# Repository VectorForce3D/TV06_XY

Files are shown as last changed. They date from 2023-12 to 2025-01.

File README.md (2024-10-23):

# TV06
## A CoreXY conversion for the Sovol SV06 designed by Terminal Velocity

The TV06 is a conversion project aimed at bringing high speeds to SV06 3D printer owners. Originally developed as a branch of the ProosaXY, the TV06 has taken on a fully unique form now as it moves into full release. The goal of the machine is simple; 10k acceleration and 250mm/s print speeds at quality. While we have blown past these speeds now, we are working to improve kinematics to achieve even higher goals.

TV06r2_Front

## Discord
Please feel free to join our ever growing community. There are lots of help resources as well as experienced members ready to assist you with your build.
https://discord.gg/thxyRm7x9U

## Documentation
[WIP](https://terminal-velocity-knowledge-base.gitbook.io/tv06)

## File Nomenclature: A warning!
All of the files enclosed in the repo are titled very specifically! You MUST follow the instructions in each items title to achieve proper results. Failing to do so is likely to result in lots of failed prints and broken parts. 

### Key:
- STR = High strength profile; 3 walls @ 150% line width, 25% gyroid infill, 3 tops and bottoms, 0.4 nozzle is reccommended for proper fitment
- STD = Standard profile; print at your standard settings
- SUP = Enable Supports; we are doing our best to eliminate supports but are not quite there yet 
- NOSUP = Turn supports off
- AC/MAIN = Denotes accent color or main color
- 0X = Quantity of that model

### Example: Beam_R_STR_NOSUP_MAIN_4X.stl
This would denote a part that requires the high stength print profile and doesn't require support. Additionally, it is the main filament color of your choosing and you need to print four of them to satisfy this items requirement.

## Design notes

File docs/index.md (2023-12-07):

# TV06 CoreXY Conversion

The Terminal Velocity 06 project is a conversion project aimed at bringing high speeds to SV06 3D printer owners. Originally developed as a branch of the ProosaXY, the TV06 has taken on a fully unique form now as it moves into the Beta testing stage. The goal of the machine is simple; 10k acceleration and 250mm/s print speeds at quality.

TV06Transparent

The TV06 was designed by Dustmuffins and Ghoste of the TV06 Discord Server. We welcome all to our community and invite you to join our wonderful [community!](https://discord.gg/xVtU45zTrk).

???+ warning "Irreversible Alterations"

     The TV06 Project seeks to integrate numerous components from the original SV06 machine line, but certain compromises are unavoidable. Specifically, some elements, such as rods and leadscrews, will be cut during the modification process. The frame predominantly consists of new metal, and proficiency in using a metal saw is essential. If you lack experience in operating a metal saw, please reach out to our help-desk channel on [Discord](https://discord.gg/xVtU45zTrk), and someone will help you out.

## A thank you to our predecessor 

The TV06 project would not be where it is today without the initial time investments of the [ProosaXY](https://www.printables.com/model/518614-proosaxy-mk3s-to-corexy-conversion). We would like to thank Chip for their incredible work and inspiring us to make this project. 

Thank You

- TV06 Team

## Support Us

We couldn't do this without the love and support of our dedicated community! While we will never ask, donations are greatly accepeted and go directly to the TV06 project and furthering its development.

[Buy us a KoFi!](https://ko-fi.com/dustmuffins){ .md-button }

## Let's get started!

We're just as excited as you to get this build underway. We thank you for showing interest in our hardwork and without further ado, Let's Go!

[I'm Ready!](about.md){ .md-button .md-button--primary }

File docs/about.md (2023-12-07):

# First Steps

The first step to getting started with this build is understanding the filename nomenclature. We have specifically encoded every filename with a set of identifiers to ensure you print everything properly and in the correct color. 
We all know aesthetics are more important than function! Right?

## Nomenclature Key

| Key | Outcome |
| :---: | :---: |
| `STR` | High strength profile  |
| `STD` |  Standard profile |
| `SUP` | Enable Supports |
| `NOSUP` | Turn supports off |
| `AC/MAIN` | Denotes accent color or main color |
| `#X` | Quantity |

???+ info "High Strength vs Standard Strength"

    We recommend 2 Walls with 150% line width, 3 tops and bottoms with 0.20mm layer height, and 25% gyroid infill for our high strength parts. We are aware that old habits die hard and the Voron print specification is also acceptable, however we recommend trying ours as all parts were tested with these settings and not Voron specifications. Standard strength denotes 2-3 walls at standard line widths and enough tops, bottoms, and infill to not have any holes or pillowing. 

## Material Choice

We can not stress this enough; ASA is the material of choice for this machine. ABS is also just as acceptable however we have found ASA to be easier to print than ABS. Polymaker makes incredible ASA that has served us well across the duration of this project. Slightly pricier than others, it is absolutely worth the quality. If you are looking for a sightly more budget oriented option, flashforge makes decent ASA as well.

???+ danger "Do NOT Cut Corners"

    The above information is all to be followed to the letter. Do not risk damage to machine, property, or personal injury because you wanted to save a relatively insignificant amount of money by purchasing PLA, PETG, or not printing the parts at proper strength settings. Additionally, do not purchase white ASA or ABS from any brand. The pigment contains titanium dioxide which is known to weaken plastics noticeably. In conjunction with this, avoid eSun ABS+ for similar reasons. These will all come back to haunt you down the road and will significantly impact the longevity and performance of your machine.

    It is not worth the risk.

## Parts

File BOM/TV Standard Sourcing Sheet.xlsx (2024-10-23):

Category | Part | Qty | Specification | Link #1 | Link #2 | Link #3 | Description
Frame | 400mm 2020 Extrusion | 9 | Any Profile | https://us.misumi-ec.com/vona2/detail/110302683830/ | https://www.amazon.com/dp/B09SGNG9C6?ref=ppx_yo2ov_dt_b_product_details&th=1 |  | Main frame components
Frame | 330mm 2020 Extrusion | 4 | Any Profile | https://us.misumi-ec.com/vona2/detail/110302683830/ | https://www.amazon.com/dp/B09SGNG9C6?ref=ppx_yo2ov_dt_b_product_details&th=1 |  | Main frame components
Frame | 310mm 2020 Extrusion | 2 | Any Profile | https://us.misumi-ec.com/vona2/detail/110302683830/ | https://www.amazon.com/dp/B09SGNG9C6?ref=ppx_yo2ov_dt_b_product_details&th=1 |  | Main frame components
Frame | 500mm 2020 Extrusion | 2 | Any Profile | https://us.misumi-ec.com/vona2/detail/110302683830/ | https://www.amazon.com/dp/B09SGNG9C6?ref=ppx_yo2ov_dt_b_product_details&th=1
Frame | 370mm 2020 Extrusion | 2 | Any Profile | https://us.misumi-ec.com/vona2/detail/110302683830/ | https://www.amazon.com/dp/B09SGNG9C6?ref=ppx_yo2ov_dt_b_product_details&th=1 |  | Main frame components
Frame | 200mm 2020 Extrusion | 2 | Any Profile | https://us.misumi-ec.com/vona2/detail/110302683830/ | https://www.amazon.com/dp/B09SGNG9C6?ref=ppx_yo2ov_dt_b_product_details&th=1 |  | Main frame components
Frame | 338mm Mellow Carbon Tube | 1 | Mellow Vz 235 | [Link too long, click me] (https://www.aliexpress.us/item/3256804164357594.html) |  |  | X Gantry
Frame | Or
Frame | 338mm 2020 Misumi Profile | 1 | Misumi | https://us.misumi-ec.com/vona2/detail/110302683830/ |  |  | X Gantry Alternative
Hardware | M5x8 Button Head | 24 | Button Head | [Link too long, click me] (https://www.aliexpress.us/item/2251832624537980.html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) | Screws On Ali (https://www.aliexpress.us/item/2251832624537980.html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) |  | Frame Hardware
Hardware | M5x20 Button Head | 4 | Button Head | [Link too long, click me] (https://www.aliexpress.us/item/2251832624537980.html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) | Screws On Ali (https://www.aliexpress.us/item/2251832624537980.html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) |  | Frame Hardware
Hardware | M5x12 Socket Head Cap | 8 | Socket Cap | [Link too long, click me] (https://www.aliexpress.us/item/3256803421528528.html) | Screws On Ali (https://www.aliexpress.us/item/2251832624557792.html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)
Hardware | M5x35 Socket Head Cap | 8 | Socket Cap | [Link too long, click me] (https://www.aliexpress.us/item/3256803421528528.html) | Screws On Ali (https://www.aliexpress.us/item/2251832624557792.html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)
Hardware | M5x16 Socket Head Cap | 4 | Socket Cap | [Link too long, click me] (https://www.aliexpress.us/item/3256803421528528.html) | Screws On Ali (https://www.aliexpress.us/item/2251832624557792.html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)
Hardware | M4x12 Socket Head Cap | 12 | Socket Cap | [Link too long, click me] (https://www.aliexpress.us/item/3256803421528528.html) | Screws On Ali (https://www.aliexpress.us/item/2251832624557792.html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)
Hardware | M4x8 Socket Head Cap | 76 | Socket Cap | [Link too long, click me] (https://www.aliexpress.us/item/3256803421528528.html) | Screws On Ali (https://www.aliexpress.us/item/2251832624557792.html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)
Hardware | M3x8 Socket Head Cap | 150 | Socket Cap | [Link too long, click me] (https://www.aliexpress.us/item/3256803421528528.html) | Screws On Ali (https://www.aliexpress.us/item/2251832624557792.html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)
Hardware | M3x10 Socket Head Cap | 45 | Socket Cap | [Link too long, click me] (https://www.aliexpress.us/item/3256803421528528.html) | Screws On Ali (https://www.aliexpress.us/item/2251832624557792.html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)
Hardware | M3x12 Socket Head Cap | 26 | Socket Cap | [Link too long, click me] (https://www.aliexpress.us/item/3256803421528528.html) | Screws On Ali (https://www.aliexpress.us/item/2251832624557792.html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)
Hardware | M3 Assortment | 1 | Socket Cap | https://a.co/d/0elFNilK
Hardware | M4 Assortment | 1 | Socket Cap | https://a.co/d/04KYN5Kn
Hardware | M3x12 Flat Head | 4 |  | Provided
Hardware | M3x8 Flat Head | 2 |  | Provided
Hardware | M3 HeatSet | 100 | OD 4.5 / L 4 | [Link too long, click me] (https://www.aliexpress.us/item/3256804349544912.html)
Hardware | M4 HeatSet | 50 | OD 5.5 / L 4 | [Link too long, click me] (https://www.aliexpress.us/item/3256804349544912.html)
Hardware | M5 HeatSet | 20 | OD 7 / L 5 | [Link too long, click me] (https://www.aliexpress.us/item/3256804349544912.html)
Hardware | M3 T Nut Hammerhead | 150 | ISO 20 | [Link too long, click me] (https://www.aliexpress.us/item/3256803706450684.html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)
Hardware | M4 T Nut Hammerhead | 100 | ISO 20 | [Link too long, click me] (https://www.aliexpress.us/item/3256803706450684.html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)
Electronics | Mainboard | 1 | Sovol | Provided
Electronics | 4010 Radial Fan | 1 | Sovol | Provided |  |  | Hotend Fan
Electronics | 350w PSU | 1 | Sovol | Provided
Electronics | Nema 17 Drive Motors | 4 | Sovol | Provided
Electronics | SV06 Toolhead | 1 | Sovol | Provided
Electronics | Extended Z Stepper Y Cable | 1 | JST-XH | [Link too long, click me] (https://www.aliexpress.us/item/3256805055141467.html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)
Electronics | GDSTime 5015 Blower | 2 | 12v/24v | [Link too long, click me] (https://www.aliexpress.us/item/2251832587030279.html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) | [Link too long, click me] (https://www.amazon.com/GDSTIME-Brushless-Bearing-Cooling-Extruder/dp/B0B1V6JTB8) |  | Cooling Fan
Motion | 400mm 8mm linear rod | 2 | Sovol | Provided
Motion | SV06 X Linear Rods | 2 | Sovol | Provided
Motion | SV06 Y Linear Rod | 2 | Sovol | provided
Motion | Fushi F695 Bearing | 2 | 10 Pack | [Link too long, click me] (https://www.aliexpress.us/item/2251832664674464.html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) | [Link too long, click me] (https://www.amazon.com/F695-2RS-Bearing-5x13x4mm-Miniature-Bearings/dp/B07VMJLXLH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) |  | Idlers
Motion | GT2 Idler Toothed | 2 | W 7mm with t | [Link too long, click me] (https://www.aliexpress.us/item/2251832836818881.html) |  |  | Idlers
Motion | 5M GT2 6mm Belt | 1 | L5M W6mm | [Link too long, click me] (https://www.aliexpress.us/item/3256806321466333.html?gatewayAdapt=glo2usa4itemAdapt) | https://www.amazon.com/Upgrade-Non-Slip-Version-Printer-Printers/dp/B08R93QQ8Z |  | Drive Belt
Motion | LM8UU Linear Bearing | 4 | Sovol | Provided | Fushi Bearings [OUR CHOICE] (https://www.aliexpress.us/item/2251832657203612.html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) |  | Z Bearings
Motion | LM8LUU Linear Bearing | 2 | Fushi | Fushi Bearings [OUR CHOICE] (https://www.aliexpress.us/item/2251832692290166.html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) | https://www.amazon.com/Printer-Bearings-JGAurora-LM08LUU-LM8LUU/dp/B083XQTH41 |  | Y Bearings
Motion | 235mm Heated Bed Assembly | 1 | Sovol | Provided | New Bed if needed (https://www.aliexpress.us/item/3256805691880025.html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)
Motion | MGN9H 300mm Linear Rail | 1 | Z1 or Z2 Preload | CNA Rails (https://www.aliexpress.us/item/2251832586981749.html) | West3D Berserker [OUR CHOICE] (https://west3d.com/products/west3d-printing-mgn9h-1r-300-350-400-linear-rails-with-carriages-cna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) | Youmetong Rails (https://www.aliexpress.us/item/3256801245010834.html?scm_id=1007.24625.271276.0&scm-url=1007.24625.271276.0) | X Axis
Filament | 2kg ASA | 1 | Main Color | https://us.polymaker.com/products/polylite-asa | https://www.amazon.com/FLASHFORGE-Filament-Dimensional-Accuracy-Printing/dp/B09V7HG9DR |  | Printed Parts
Filament | 1kg ASA | 1 | Accent Color | https://us.polymaker.com/products/polylite-asa | https://www.amazon.com/FLASHFORGE-Filament-Dimensional-Accuracy-Printing/dp/B09V7HG9DR |  | Printed Parts

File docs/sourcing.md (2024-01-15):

## It's Alive!
This sourcing guide is a living, breathing document and should be viewed as such. The purpose of the sourcing guide is to help builders to locate parts as quickly and easily as possible. We understand that links go dead quite often as sellers pull and relist listings all the time. Please report any issues with seller links you find directly to us under the dead-links channel in our discord.

???+ warning "We're not finished!"

    This is NOT currently an exhaustive list of components. We are working towards this, but this takes time. We have limited resources and this is certainly a WIP. 

<div style="text-align: center"><iframe src="https://docs.google.com/spreadsheets/d/e/2PACX-1vRDuzh9zTTb0Dr3VAwCe3eVq7Pyc6kqRn8ZqNsRaBrNnAQ9p_Byug8odcZ4Mtml6v6jA4KULE2Pz__y/pubhtml;headers=false" frameborder="0" width="100%" height="1000" scrolling="no"></iframe></div>

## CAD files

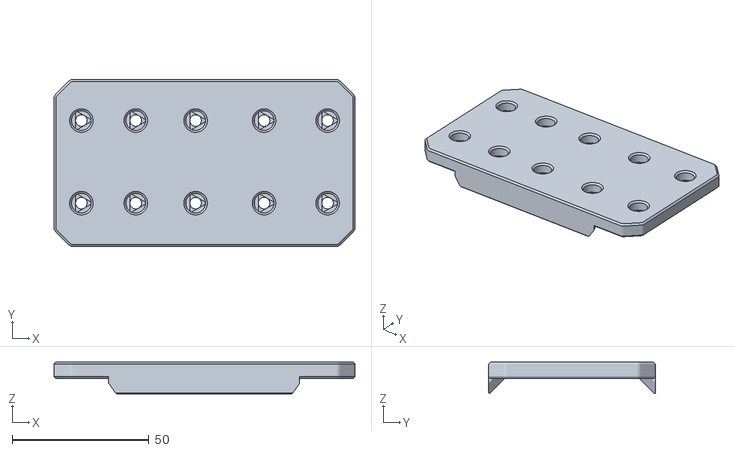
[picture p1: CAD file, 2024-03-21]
STL/Gantry/B_Drive/MotorMountRetensionPlate[B]_STR_NOSUP_MAIN_1X.STL
110.0 x 61.0 x 11.6

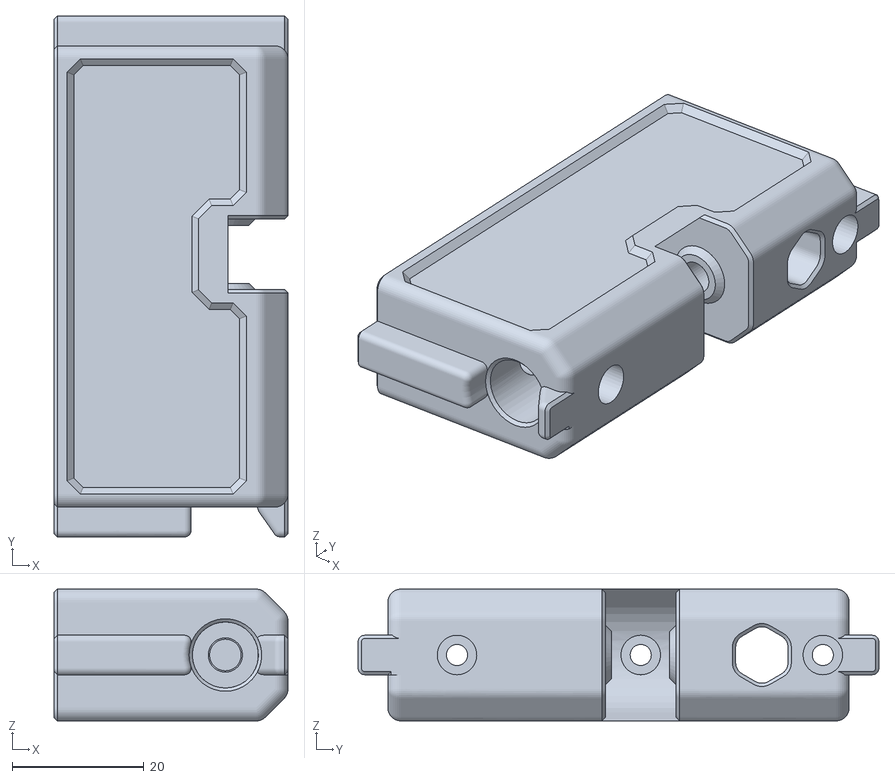
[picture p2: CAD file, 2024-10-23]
STL/Gantry/frontidlertower_r_str_nosup_main_1x.stl
35.5 x 79.0 x 20.0

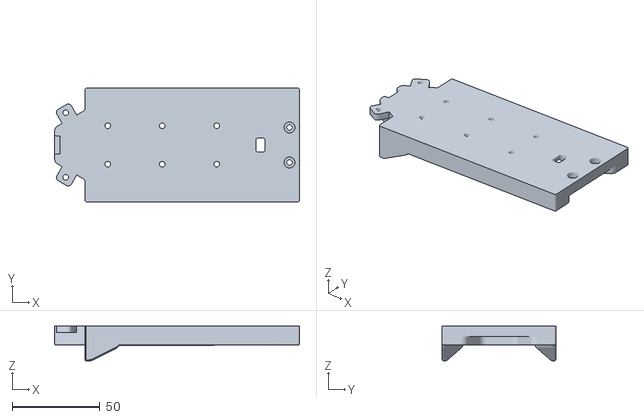
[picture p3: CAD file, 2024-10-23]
STL/Skirts/sideskirt_std_nosup_main_2x.stl
140.0 x 65.0 x 20.0

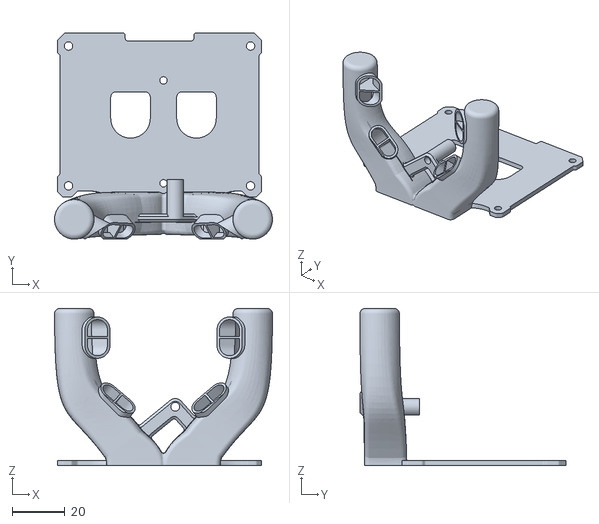
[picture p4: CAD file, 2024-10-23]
STL/Toolhead/QuadroDuct_Short_STR_SUP_MAIN_1X.stl
82.6 x 78.1 x 59.6

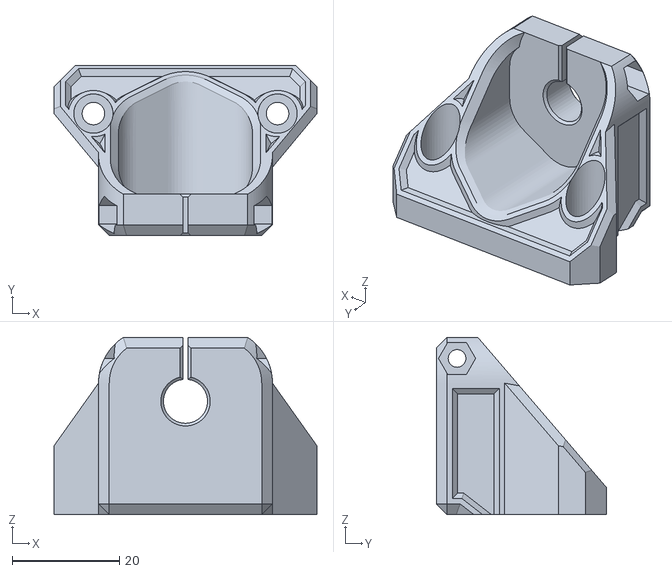
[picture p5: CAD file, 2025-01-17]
STL/Z_Assembly/lowerrodmount_str_nosup_main_4x.stl
49.0 x 31.8 x 33.0

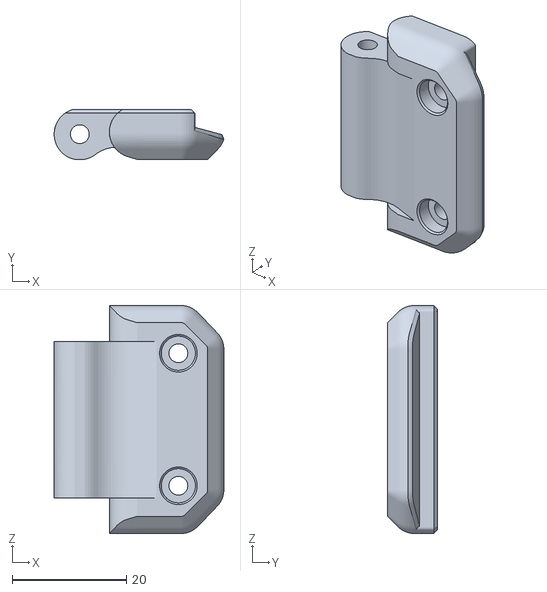
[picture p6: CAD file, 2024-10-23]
STL/Enclosure/hingebody_str_nosup_main_4x.stl
29.8 x 8.71 x 40.0

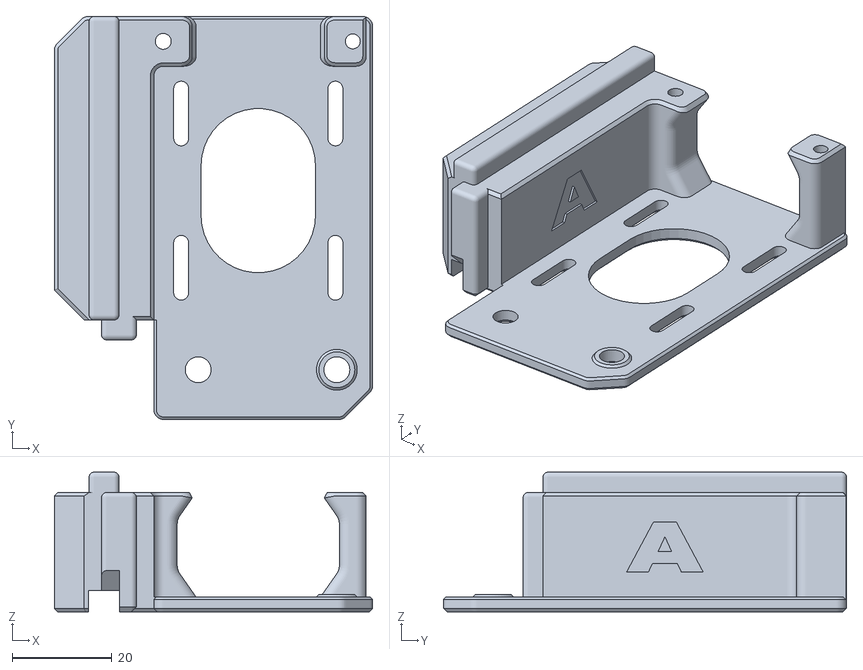
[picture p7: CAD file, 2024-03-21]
STL/Gantry/A_Drive/MotorPlate_Mid_A_Drive_STR_NOSUP_MAIN_1X.STL
64.0 x 81.0 x 28.1

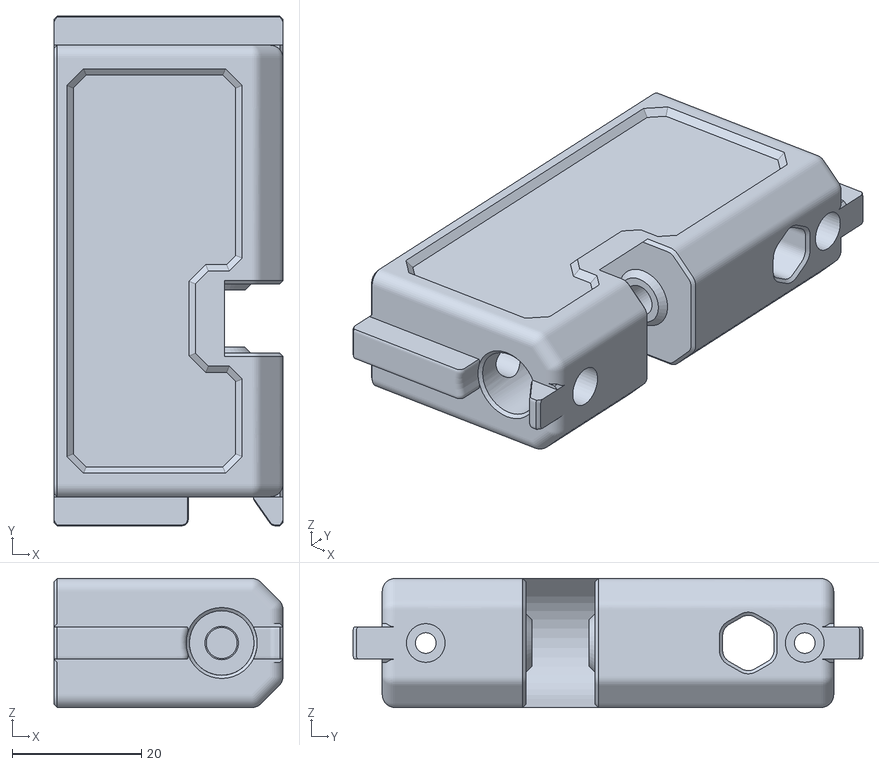
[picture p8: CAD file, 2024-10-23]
STL/Gantry/frontidlertower5mm_l_str_nosup_main_1x.stl
35.5 x 79.0 x 20.0

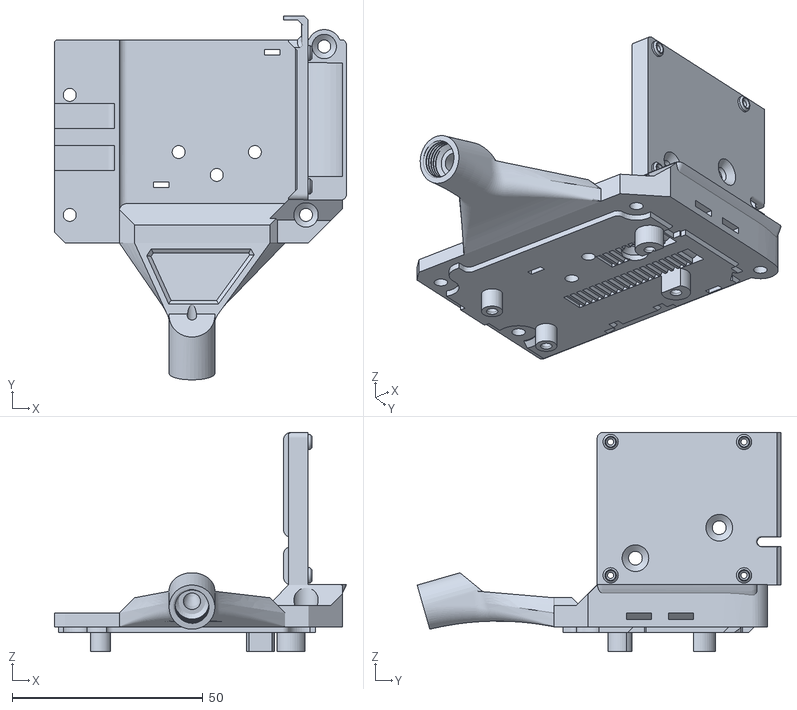
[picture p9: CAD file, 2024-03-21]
STL/Toolhead/BodyPlate_STR_SUP_MAIN_1X.STL
76.6 x 95.4 x 57.5

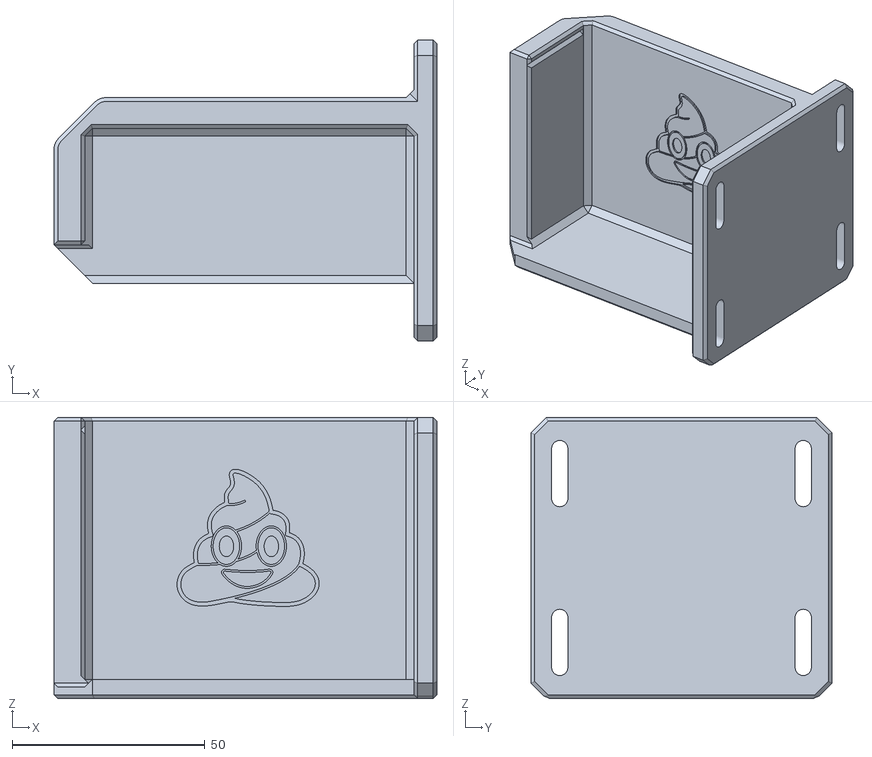
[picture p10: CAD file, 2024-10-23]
STL/Frame/purge_bucket_mount2_str_main_1x.stl
99.4 x 78.2 x 73.0

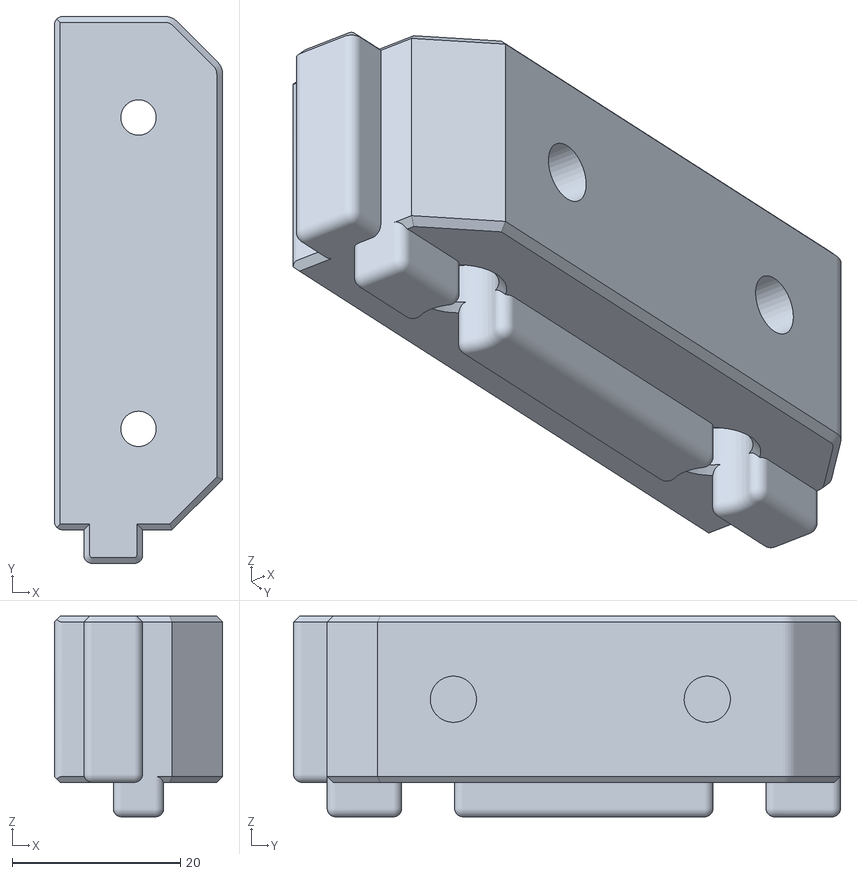
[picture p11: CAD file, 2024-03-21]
STL/Gantry/A_Drive/MotorPlate_Bottom_A_Drive_STR_NOSUP_MAIN_1X.STL
20.0 x 65.0 x 23.8

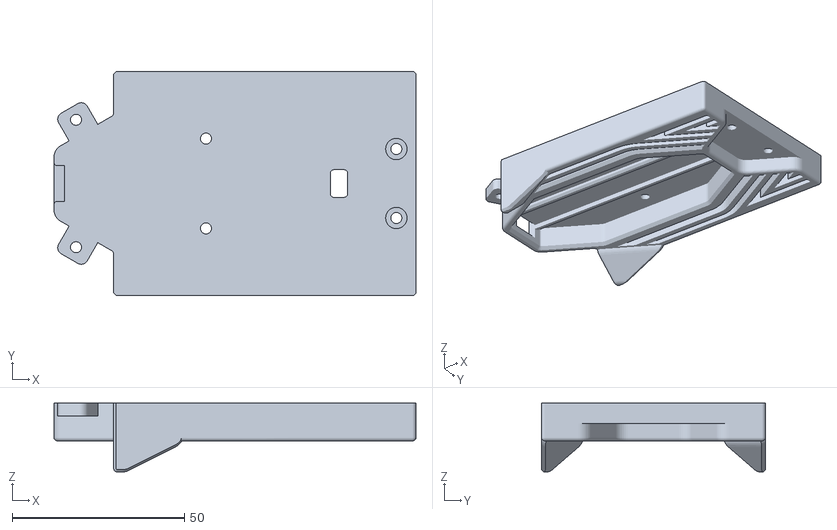
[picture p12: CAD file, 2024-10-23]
STL/Skirts/frontskirt_std_nosup_main_2x.stl
105.0 x 65.0 x 20.0

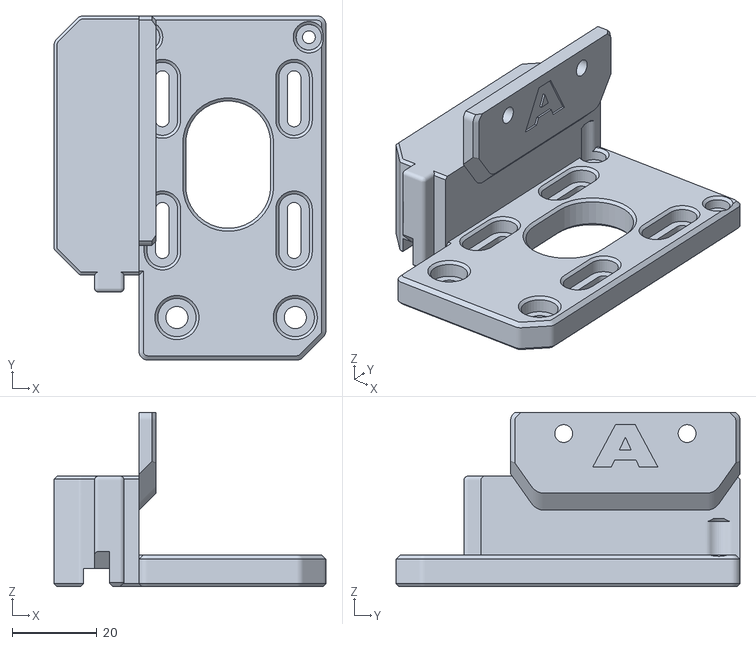
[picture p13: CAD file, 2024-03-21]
STL/Gantry/A_Drive/MotorPlate_Top_A_Drive_STR_NOSUP_MAIN_1X.STL
64.0 x 81.0 x 41.1

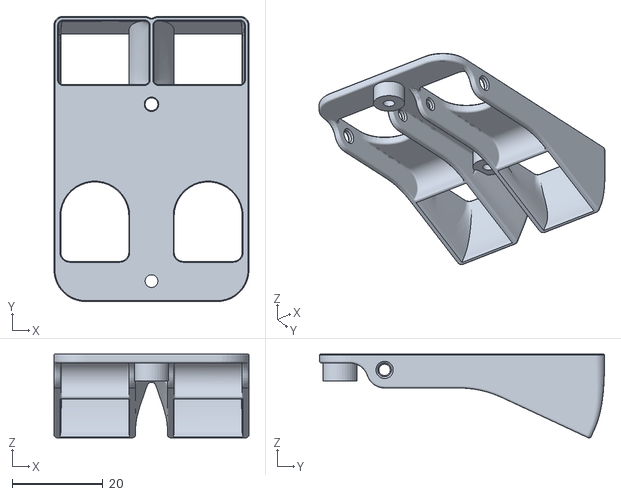
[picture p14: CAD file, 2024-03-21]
STL/Toolhead/Dual5015Mount_STR_NOSUP_MAIN_1X.STL
43.0 x 62.9 x 18.5

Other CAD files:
STL/Gantry/B_Drive/MotorPlate_Bottom_B_Drive_STR_NOSUP_MAIN_1X.STL
STL/Gantry/frontidlertower_l_str_nosup_main_1x.stl
STL/Gantry/B_Drive/MotorPlate_Top_B_Drive_STR_NOSUP_MAIN_1X.STL
STL/Gantry/frontidlertower5mm_r_str_nosup_main_1x.stl
DXF/TV06R2_Panels.step
DXF/[1x][ACM]Floor_Panel.dxf
DXF/[1x][ACM]Rear_Panel.dxf
DXF/[1x][PC_ACR]Top_Panel.dxf
DXF/[2x][PC_ACR]Door_Panel.dxf
DXF/[2x][PC_ACR]Side_Panel.dxf
STL/AWD/11mm_Spacer_2X.stl
STL/AWD/1mm_Spacer_10X.stl
STL/AWD/6mm AWD XY joint right a.stl
STL/AWD/6mm AWD XY joint right b.stl
STL/AWD/6mm AWD XY joint right c.stl
STL/AWD/FL_Bottom.stl
STL/AWD/FL_Top.stl
STL/AWD/FR_Bottom.stl
STL/AWD/FR_Top.stl
STL/AWD/Pin_Support_2X.stl
STL/AWD/RL_Bottom.stl
STL/AWD/RL_Top.stl
STL/AWD/RR_Bottom.stl
STL/AWD/RR_Top.stl
STL/AWD/Tensioner_2X.stl
STL/AWD/Y_Car_1_2X.stl
STL/AWD/Y_Car_2_2X.stl
STL/AWD/Y_Car_3_2X.stl
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

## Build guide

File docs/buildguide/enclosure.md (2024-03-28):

## Enclosure Design

Enclosure

## Bill of Materials
   | Item | Name | Quantity |
   | :---: | :---: | :----: |
   | `1` | M3x8 SHCS | 27 |
   | `2` | M3x10 SHCS | 12 |
  | `3` | M3x12 SHCS | 8 |
  | `4` | PanelClamp.stl | 27 |
   | `5` | Enclosure Door | 2 |
   | `6` | Enclosure Side Panel | 2 |
  | `7` | Enclosure Top Panel | 1 |
  | `8` | Enclosure Rear Panel | 1 |

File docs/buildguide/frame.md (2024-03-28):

## Frame Design
We created our frame to be simple and straightforward, eliminating the need for brackets or obscure corner attachments. Instead, we opted for blind joints because of their exceptional strength and rigidity. What sets them apart is not just their performance but also their affordability—a high-strength option at a low cost.

Frame

???+ warning "Buy The Right Extrusion!"

    Not all aluminum extrusion is created equally. Check your suppliers profile dimensions for the inner circular whole diameter. This MUST be smaller than 5mm so that we are able to tap the whole for an M5 thread which is about 4.8mm wide. 4.2mm hole is the prefered outer diameter of the center hole.

## Bill of Materials
=== "Carbon X Gantry"

    | Item | Name | Quantity |
    | :---: | :---: | :----: |
    | `1` | 400mm 2020 Extrusion | 9 |
    | `2` | 330mm 2020 Extrusion | 4 |
    | `3` | 310mm 2020 Extrusion | 2 |
    | `4` | 500mm 2020 Extrusion | 2 |
    | `5` | 370mm 2020 Extrusion | 2 |
    | `6` | 200mm 2020 Extrusion | 2 |
    | `7` | 338mm Mellow Carbon Tube | 1 |
    | `8` | M5x8 Button Head | 30 |
    | `9` | M5x20 Button Head | 4 |
    | `10` | M4x8 Socket Head Cap | 4 |
    
=== "Alu Tube X Gantry"

    | Item | Name | Quantity |
    | :---: | :---: | :----: |
     | `1` | 400mm 2020 Extrusion | 9 |
    | `2` | 330mm 2020 Extrusion | 4 |
    | `3` | 310mm 2020 Extrusion | 2 |
    | `4` | 500mm 2020 Extrusion | 2 |
    | `5` | 370mm 2020 Extrusion | 2 |
    | `6` | 200mm 2020 Extrusion | 2 |
    | `7` | 300mm 20mm 2mm Wall Aluminum Square Tube | 1 |
    | `8` | M5x8 Button Head | 30 |
    | `9` | M5x20 Button Head | 4 |
    | `10` | M4x8 Socket Head Cap | 4 |

???+ info "Carbon or Alu X Gantry?"

    As of right now, we recommend everyone purchase the carbon gantry. While it does add costs, it will offer the best results. There are also seperate Y Blocks that must be used to run the Alu gantry.

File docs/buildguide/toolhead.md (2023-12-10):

## What's new?
The SV06 is known for it's superior extrusion quality and compact toolhead size. We reused the stock toolhead with some modified parts to ensure that we brought this pedigree of perfection over to our machine. Namely, a major cooling upgrade was due for these increased speeds.

Toolheadfixed
## Bill of Materials
=== "Dual 5015"

    | Item        | Name | Quantity | Printable |
    | :---------: | ---- | :--: | ---- |
    | `1` | SV06 Stock Extruder | 1 | No |
    | `2` | [BackBeltPlate_STR_NOSUP_ANY_1X.stl](https://github.com/VectorForce3D/TV06_XY/raw/main/STL/Toolhead/BackBeltPlate_STR_NOSUP_ANY_1X.stl) | 1 | Yes |
    | `3` | [Double5015Mount_STD_NOSUP_MAIN_1X.stl](https://github.com/VectorForce3D/TV06_XY/raw/main/STL/Toolhead/Double5015Mount_STD_NOSUP_MAIN_1X.stl) | 1 | Yes |
    | `4` | MGN9H 300mm | 1 | No |
    | `5` | [ExtruderMount_STR_SUP_MAIN_1X.stl](https://github.com/VectorForce3D/TV06_XY/raw/main/STL/Toolhead/ExtruderMount_STR_SUP_MAIN_1X.stl) | 1 | Yes |
    | `6` | [FrontBeltPlate_STR_NOSUP_AC_1X.stl](https://github.com/VectorForce3D/TV06_XY/raw/main/STL/Toolhead/FrontBeltPlate_STR_NOSUP_AC_1X.stl) | 1 | Yes |
    | `7` | [MonolithicRailMount_STR_NOSUP_AC_1X.stl](https://github.com/VectorForce3D/TV06_XY/raw/main/STL/Toolhead/MonolithicRailMount_STR_NOSUP_AC_1X.stl) | 1 | Yes |
    | `8` | [StockNozzleAirDuct_STD_NOSUP_MAIN_1X.stl](https://github.com/VectorForce3D/TV06_XY/raw/main/STL/Toolhead/StockNozzleAirDuct_STD_NOSUP_MAIN_1X.stl) | 1 | Yes |
    | `9` | M3x12 Flathead | 4 | No |
    | `10` | M3x8 | 5 | No |
    | `11` | M3x8 Flathead | 2 | No |
    | `12` | M3x12 Flathead | 4 | No |
    | `13` | GDSTime 5015 12v Blower | 2 | No |

=== "4028 Radial Fan"

    | Item        | Name | Quantity | Printable |
    | :---------: | ---- | :--: | ---- |
    | `1` | SV06 Stock Extruder | 1 | No |
    | `2` | [BackBeltPlate_STR_NOSUP_ANY_1X.stl](https://github.com/VectorForce3D/TV06_XY/raw/main/STL/Toolhead/BackBeltPlate_STR_NOSUP_ANY_1X.stl) | 1 | Yes |
    | `3` | 4028Mount.stl | 1 | Yes |
    | `4` | MGN9H 300mm | 1 | No |
    | `5` | [ExtruderMount_STR_SUP_MAIN_1X.stl](https://github.com/VectorForce3D/TV06_XY/raw/main/STL/Toolhead/ExtruderMount_STR_SUP_MAIN_1X.stl) | 1 | Yes |
    | `6` | [FrontBeltPlate_STR_NOSUP_AC_1X.stl](https://github.com/VectorForce3D/TV06_XY/raw/main/STL/Toolhead/FrontBeltPlate_STR_NOSUP_AC_1X.stl) | 1 | Yes |
    | `7` | [MonolithicRailMount_STR_NOSUP_AC_1X.stl](https://github.com/VectorForce3D/TV06_XY/raw/main/STL/Toolhead/MonolithicRailMount_STR_NOSUP_AC_1X.stl) | 1 | Yes |
    | `8` | 4028NozzleDuct.stl | 1 | Yes |
    | `9` | M3x12 Flathead | 4 | No |
    | `10` | M3x8 | 5 | No |
    | `11` | M3x8 Flathead | 2 | No |
    | `12` | M3x12 Flathead | 4 | No |
    | `13` | Uxcell 4028 24v | 1 | No |

## Assembly Guide

## Modding Guide
This toolhead is highly capable and many will find that upgrading the toolhead is not neccesary, but we know how much modding matters so we are directly supporting this. Below are the steps required to adapt any toolhead design to our belt system.

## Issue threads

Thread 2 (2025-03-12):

Firmware and cost

Cristian-O, 2025-03-12:
Hello! Is there any firmware available for the original mainboard? This project seems amazing as most parts are already there or 3d printed(compared to others). This conversion should be cheap if you keep the stock mainboard and run marlin at least for testing. Compared to Ender3-NG this can cost a lot less and be easier to assemble not to mention that most of the wiring is already done. Do you think this conversion(printer+frame) would end up less than 300 USD as it will compare to an Flashforge adventurer 5M for example with improved frame, extruder and maintenance. At 300 USD it will be comparable with SV06 ACE but with corexy and better maintenance for long term. Thank you for all the work! Hope to build one soon :)

VectorForce3D, 2025-03-12:
There is one made by Jomik. It is available on GitHub and the discord. I would recommend you go straight to klipper and not waste your time on Marlin. It can work, but it will only make life harder :). And yes, this is doable for $300 if you source it properly.

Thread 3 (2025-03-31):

Please update the documentation

arkabhowmick, 2025-03-31:
The M3x8 screw won't work on the feet.
It's too small to be attached to the 2020 frame with the hammerhead nuts.
It requires a M3x15 screw. Please update the doc.

arkabhowmick, 2025-04-07:
Some more updates:

- M4 x 20  (4 pcs) Needed for AB drives
- M3 x 14 (6pcs) is needed for front idler tower ab drives
- front idler tower should be done at the beginning when attaching the frame.
- RearBeltPlate_STR_NOSUP_MAIN_1X.stl is missing in the stl files

arkabhowmick, 2025-05-14:
Floor Panels' STL missing in the STLs folder.

arkabhowmick, 2025-05-17:
M4 x 16 pcs needed for frame braces

ac7ss, 2025-08-19:
Docs are using the old anchor_horn pieces. Please update and document the screws required to connect the compliant mechanism to the anchor_horn.

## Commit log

2023-11-30 Add files via upload
    Skirt components and feet. Rev 1
    [Foot_STRNG_SUP_4X.STL, Skirt_L_STD_NOSUP_4X.STL, Skirt_MidPlate_STD_NOSUP_2X.STL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]
2023-12-07 Delete STL/Z Assembly/AnchorHorn_STR_NOSUP_AC_2X.STL
    Update to bottom mount version
    [AnchorHorn_STR_NOSUP_AC_2X.STL]
2023-12-07 Add files via upload
    corrected LM8LUU bearing opening size
    [YCarriage_STR_SUP_AC_1X.stl]
2023-12-17 Delete STL/Frame/FrontIdlerTower_L_STR_NOSUP_MAIN_1X.STL
    had collision issues
    [FrontIdlerTower_L_STR_NOSUP_MAIN_1X.STL]
2023-12-17 Delete STL/Frame/FrontIdlerTower_R_STR_NOSUP_MAIN_1X.STL
    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
    [FrontIdlerTower_R_STR_NOSUP_MAIN_1X.STL]
2023-12-17 Delete STL/Frame/RearIdlerTower_L_STR_NOSUP_MAIN_1X.STL
    adding additional clearance on bridge
    [RearIdlerTower_L_STR_NOSUP_MAIN_1X.STL]
2023-12-17 Delete STL/Frame/RearIdlerTower_R_STR_NOSUP_MAIN_1X.STL
    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
    [RearIdlerTower_R_STR_NOSUP_MAIN_1X.STL]
2023-12-17 Add files via upload
    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
    [RearIdlerTower_L_STR_NOSUP_MAIN_1X.stl, RearIdlerTower_R_STR_NOSUP_MAIN_1X.stl]
2023-12-18 Delete STL/Frame/TensionScrewKnob_STR_SUP_AC_2X.STL
    adding a bridged version
    [TensionScrewKnob_STR_SUP_AC_2X.STL]
2023-12-18 Add files via upload
    added bridging section to make it printable without supports
    [TensionScrewKnob_STR_SUP_AC_2X.STL]
2023-12-18 Rename TensionScrewKnob_STR_SUP_AC_2X.STL to TensionScrewKnob_STR_NOSUP_AC_2X.STL
    no supports needed now
    [TensionScrewKnob_STR_NOSUP_AC_2X.STL]
2023-12-18 Delete STL/Frame/RearIdlerMount_R_STR_NOSUP_MAIN_1X.STL
    adding bridging for vertical printing option
    [RearIdlerMount_R_STR_NOSUP_MAIN_1X.STL]
2023-12-18 Delete STL/Frame/RearIdlerMount_L_STR_NOSUP_MAIN_1X.STL
    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
    [RearIdlerMount_L_STR_NOSUP_MAIN_1X.STL]
2023-12-18 Add files via upload
    added bridging option for vertical printing
    [RearIdlerMount_L_STR_NOSUP_MAIN_1X.stl, RearIdlerMount_R_STR_NOSUP_MAIN_1X.stl]
2023-12-18 Delete STL/Frame/MotorMount_R_STR_NOSUP_MAIN_1X.STL
    adding bridging on the pulley section
    [MotorMount_R_STR_NOSUP_MAIN_1X.STL]
2023-12-18 Delete STL/Frame/MotorMount_L_STR_NOSUP_MAIN_1X.STL
    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
    [MotorMount_L_STR_NOSUP_MAIN_1X.STL]
2023-12-18 Add files via upload
    adding bridged version of motor mounts and adding idler tower spacer
    [IdlerTowerSpacer_STR_NOSUP_AC_2X.stl, MotorMount_L_STR_NOSUP_MAIN_1X.stl, MotorMount_R_STR_NOSUP_MAIN_1X.stl]
2023-12-23 Delete STL/XY Motion/FrontIdlerTower_R_STR_NOSUP_MAIN_1X.STL
    Larger front idler tower and smoother homing
    [FrontIdlerTower_R_STR_NOSUP_MAIN_1X.STL]
2023-12-23 Delete STL/XY Motion/FrontIdlerTower_L_STR_NOSUP_MAIN_1X.STL
    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
    [FrontIdlerTower_L_STR_NOSUP_MAIN_1X.STL]
2023-12-23 Larger front idler tower and smoother homing
    [FrontIdlerTower_L_STR_NOSUP_MAIN_1X.stl, FrontIdlerTower_R_STR_NOSUP_MAIN_1X.stl]
2024-01-15 Delete STL/Frame/FrameBrace_STR_NOSUP_MIXED_2X.STL
    Updating to V12
    [FrameBrace_STR_NOSUP_MIXED_2X.STL]
2024-01-15 V12 Update
    [FrameBrace_STR_NOSUP_MIXED_2X.stl]
2024-01-15 Updating to V12
    [EXTRUDER_SUPPORT_STR_SUP_MAIN_1X.stl, FRONT_BELT_PLATE_STR_NOSUP_ACC_1X.stl, MonolithicRailMount_STR_NOSUP_AC_1X.stl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]
2024-01-15 Updated to V12
    [Carbon_xbeam_support_STR_NOSUP_ANY_2X.stl, FACB_PAIR_STR_NOSUP_MIXED_1X.stl, FrontIdlerTower_L_STR_NOSUP_MAIN_1X.stl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]
2024-10-17 Add files via upload
    Added individual panel files for TV06r2.1
    [[1x][ACM]Floor_Panel.dxf, [1x][ACM]Rear_Panel.dxf, [1x][PC_ACR]Top_Panel.dxf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]
